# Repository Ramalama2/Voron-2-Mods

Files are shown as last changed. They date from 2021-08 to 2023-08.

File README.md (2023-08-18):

- Hey Boys & Girls, im sorry but i won't come back and don't plan to update anything as well.
- Thats why i have Archieved this Repository now.
- That way people will clearly see, that they should not expect anything here and probably switch to another/better/newer Mods that are available in the meantime.

Otherwise, it was a great time and a great community with a lot of cool people!
Cheers :-)</h1></center>

------------------------

<h1 align="center">Mod Index:</h1>
<table align="center">
  <tr>
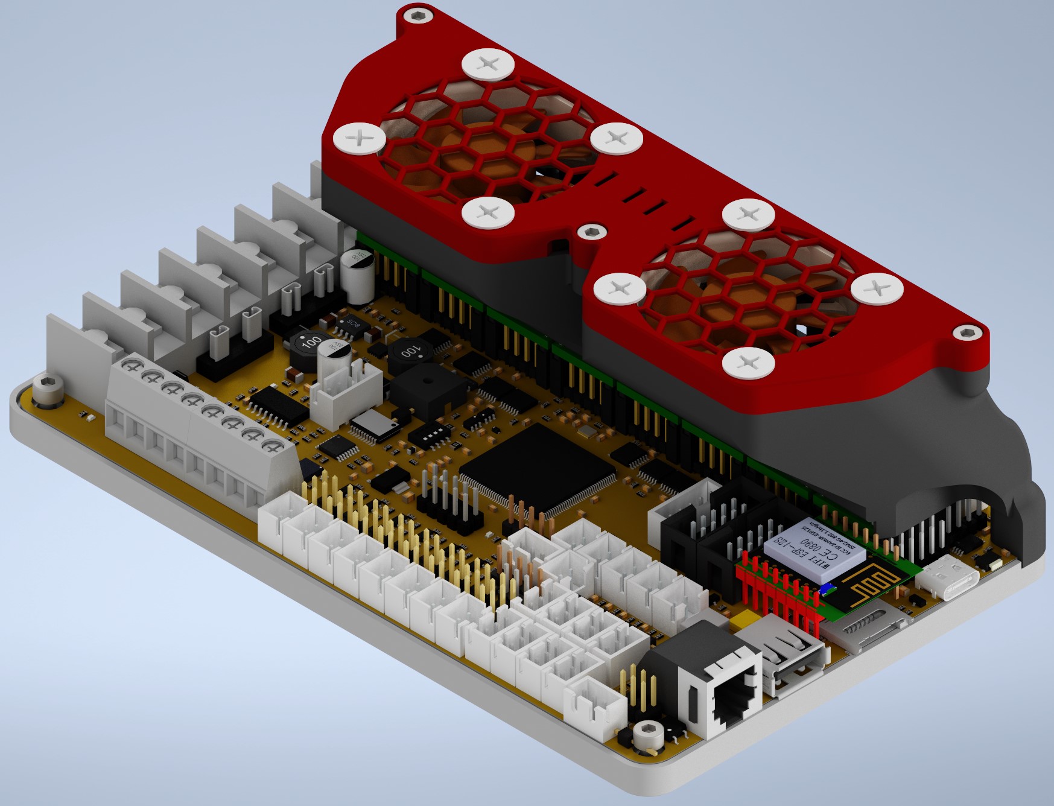
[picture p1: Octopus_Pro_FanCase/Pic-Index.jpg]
    <td align="center"><a href="./Octopus_Pro_FanCase">Octoglasses<br></a></td>
  </tr>
  <tr>
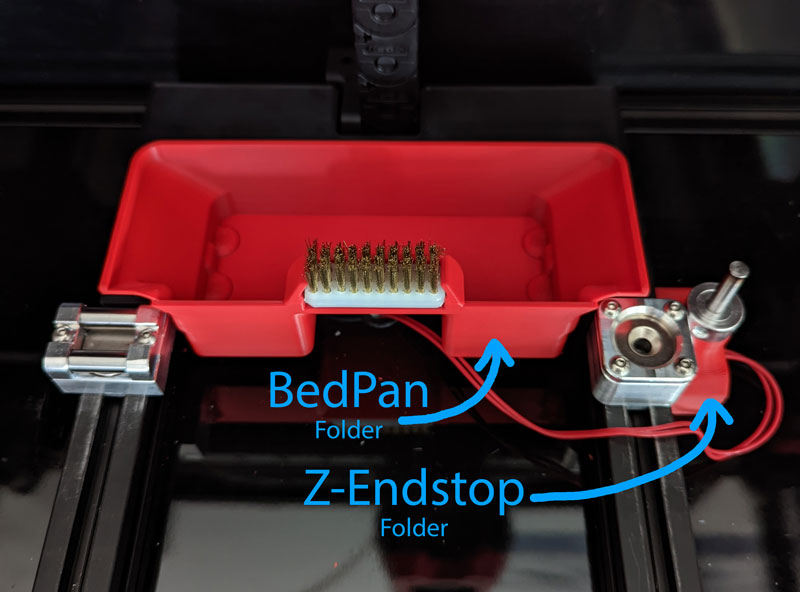
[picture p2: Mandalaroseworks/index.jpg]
    <td align="center"><a href="./Mandalaroseworks">Mandalaroseworks<br></a></td>
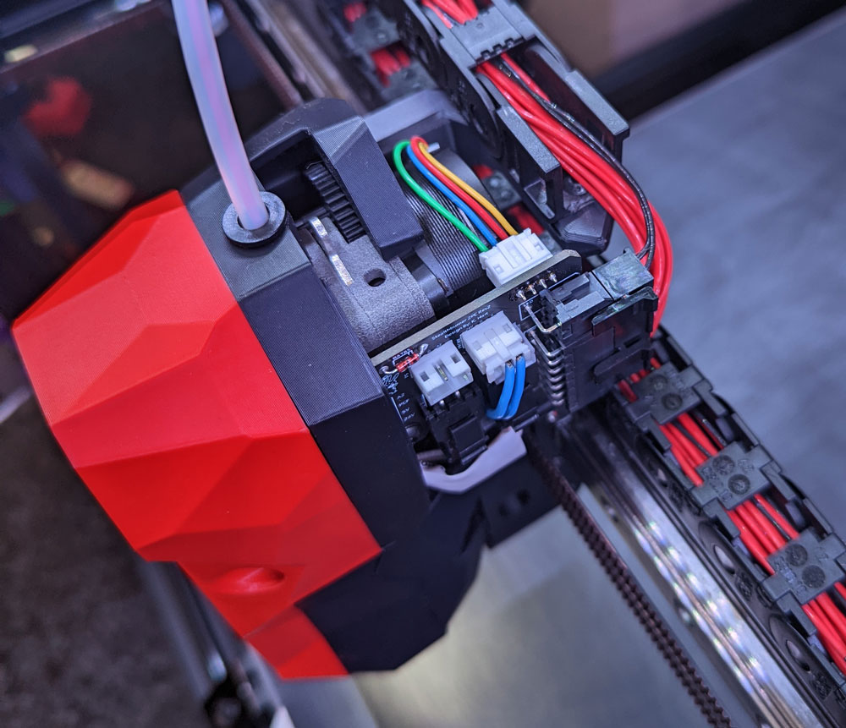
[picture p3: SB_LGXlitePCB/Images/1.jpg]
    <td align="center"><a href="./SB_LGXlitePCB">Stealthburner LGX lite<br></a></td>
  </tr>
  <tr>
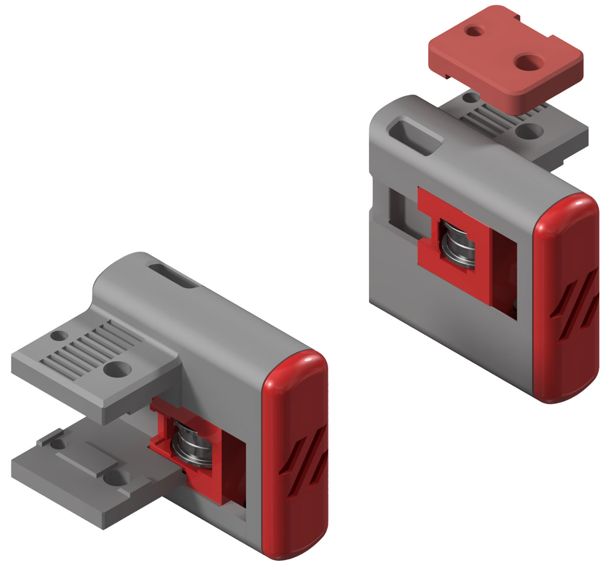
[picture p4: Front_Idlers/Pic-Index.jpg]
    <td align="center"><a href="./Front_Idlers">Front Idlers<br></a></td>
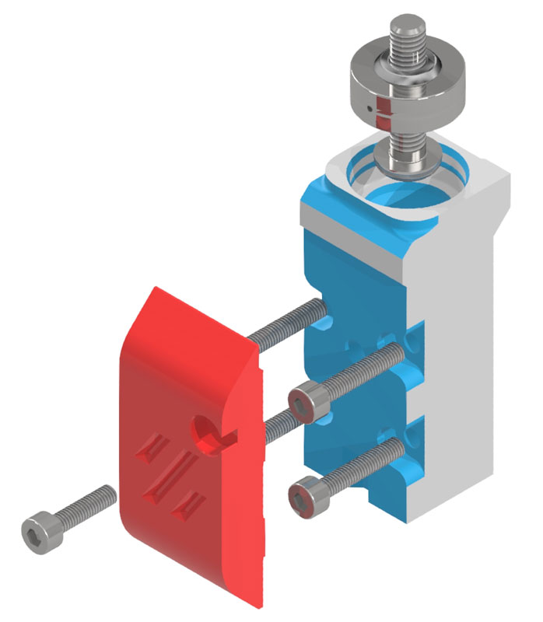
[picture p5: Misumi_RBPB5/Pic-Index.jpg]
	<td align="center"><a href="./Misumi_RBPB5">Misumi RBPB5 (GE5C Gucci Mod)<br></a></td>
  </tr> 
  <tr>
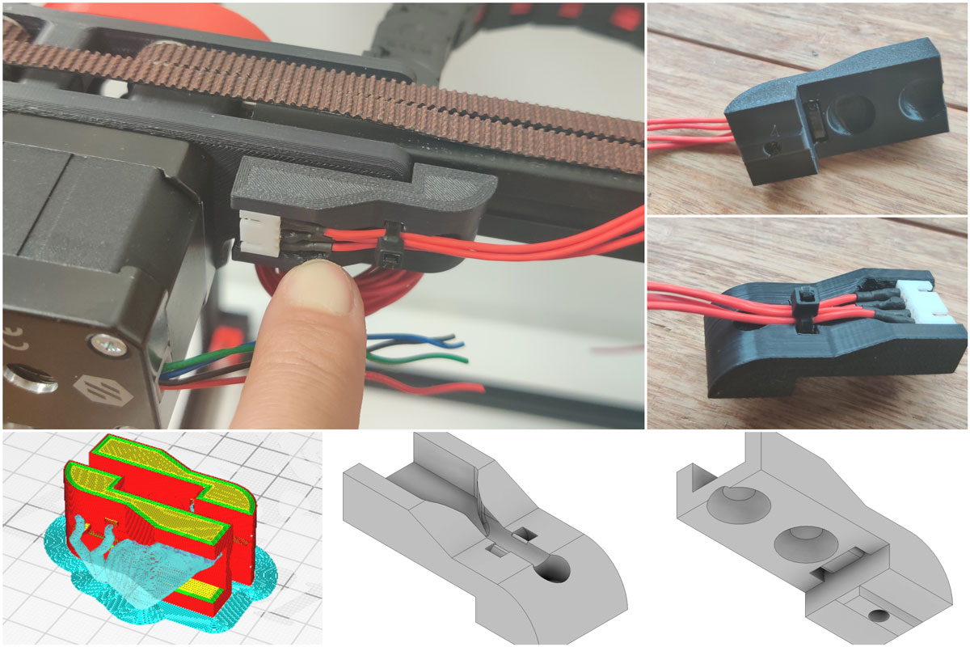
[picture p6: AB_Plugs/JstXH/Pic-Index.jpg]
    <td align="center"><a href="./AB_Plugs">AB Plugs (Jst/Microfit)<br></a></td>
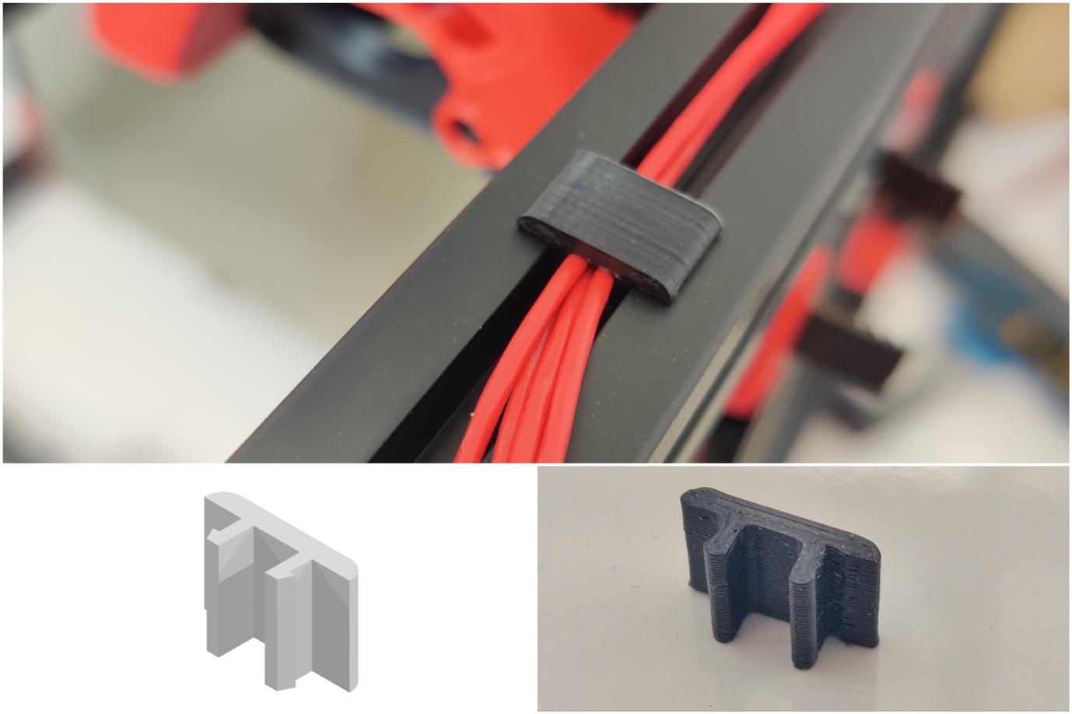
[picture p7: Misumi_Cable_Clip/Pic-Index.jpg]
	<td align="center"><a href="./Misumi_Cable_Clip">Misumi Cable Clip<br></a></td>
  </tr> 
  <tr>
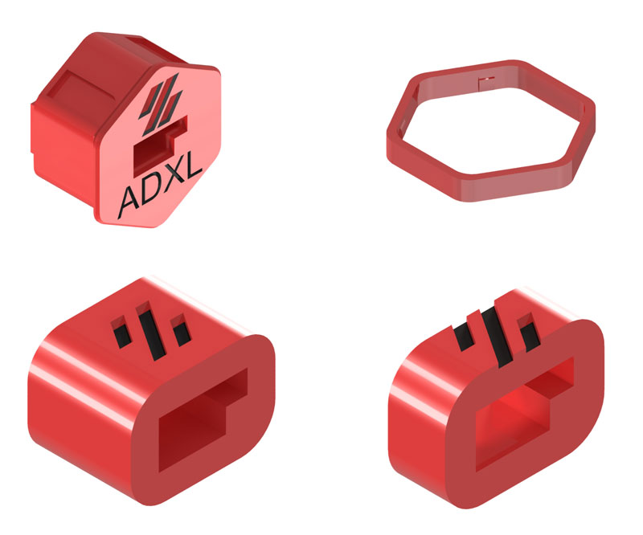
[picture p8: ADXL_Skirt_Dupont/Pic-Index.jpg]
    <td align="center"><a href="./ADXL_Skirt_Dupont">ADXL Skirt Dupont<br></a></td>
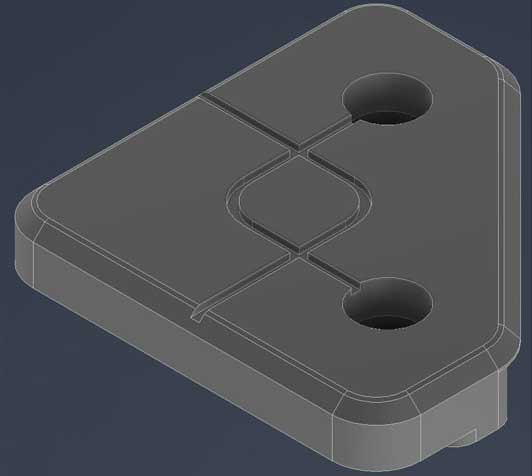
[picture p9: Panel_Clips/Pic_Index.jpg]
	<td align="center"><a href="./Panel_Clips">Panel Clips<br></a></td>
  </tr>
  <tr>
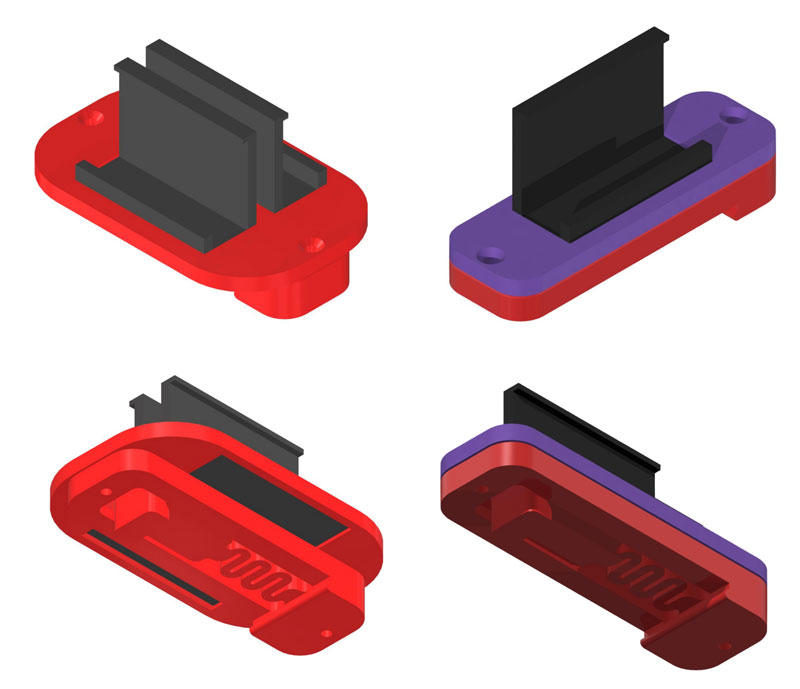
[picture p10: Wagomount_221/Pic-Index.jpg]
    <td align="center"><a href="./Wagomount_221">Wago 221 DIN Mount<br></a></td>
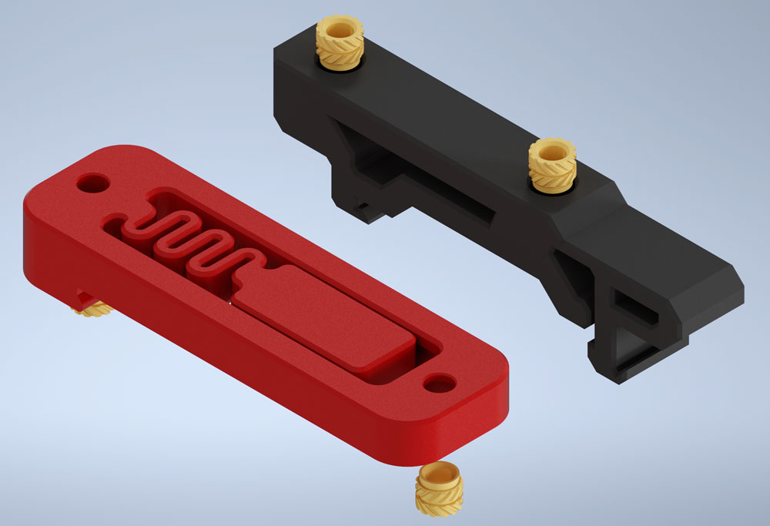
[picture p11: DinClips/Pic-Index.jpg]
    <td align="center"><a href="./DinClips">Din Clips<br></a></td>
  </tr>
    <tr>
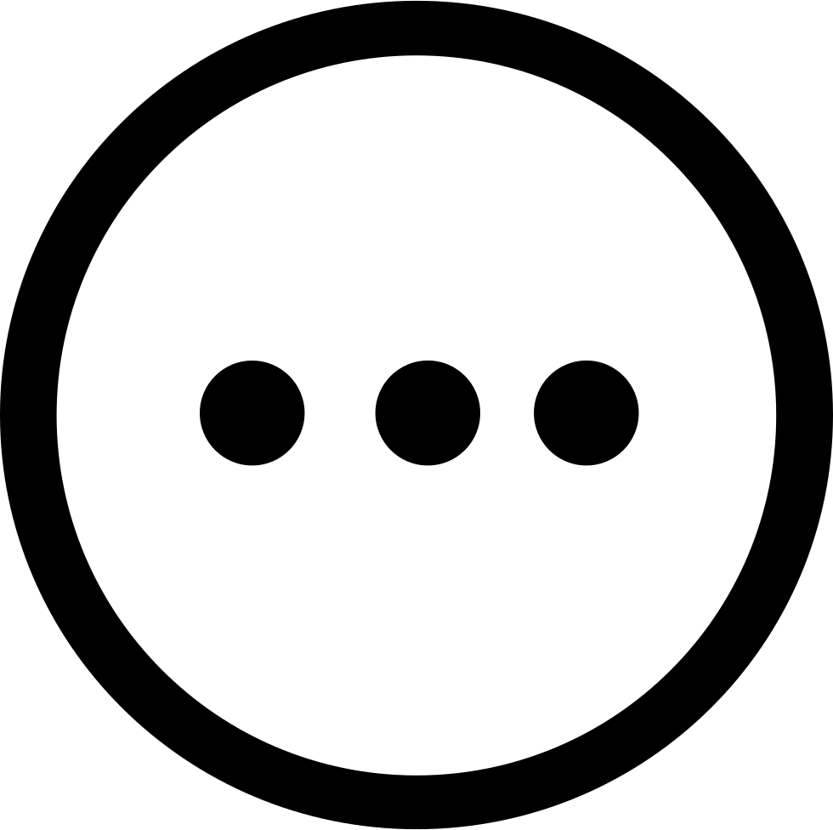
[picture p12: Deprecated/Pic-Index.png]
    <td colspan="2" align="center"><a href="./Deprecated">Deprecated Stuff<br></a></td>
  </tr>
  </table>

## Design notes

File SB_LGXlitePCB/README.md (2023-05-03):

## Changelog:
- 25.07.2022: Cable Cover, First test, please try and report back. It may be a little thin xD<br>
- 25.07.2022: <a href="./Option_without_LGXlite-FanPCB">New Option without FanPCB</a>. See this as an emergency option,<br>
this will work with the Standard FanPCB from hartk!<br>
But at least you can now get the thing running and replace later when you get the Lgx lite FanPCB.<br>
-Release (24.07.22): Release!
<details>
  <summary>
    Old Changelog
  </summary>
- Nothing yet.
</details>

#

#

#

<details>
  <summary>
    CREDITS: LOGAN!!!, Eytecz, hartk, Voron-Team & all the great people we have in our community :-)
  </summary>
* Logan: He modified hartk's Fan-PCB to make this Project working at all! Thanks Logan!!!<br>
* Eytecz: <a href="https://github.com/Eytecz/LGX_Lite_Stealthburner_CW2_style_mount">Original SB-Lgxlite</a>, he made the work, i modified it only for the 2-Part PCB!<br>
* hartk: For the beatiful 2-Part PCB :-)<br>
* Voron-Team: Yeah, without you Guys, nothing were possible here :-)<br>
* Community: Feelingwise discord is a Place filled with only nice and always helpful People! A special thanks to all of them, i personally just love everyone there!<br>
</details>

<details>
  <summary>
    Print Settings:
  </summary>
- Default Voron settings, correct orientation, no supports needed!<br>
</details>

<details>
  <summary>
    Where can i get the Fan-PCB from?:
  </summary>
- JlcPCB: All you need is the <a href="./PCB">Gerber File</a><br>
- Discord: Gi7mo!#4618 -> He has them already on Stock! (Germany/EU)<br>
- Note: The mainpcb is default hartk, only the fanpcb changed a bit!<br>
</details>

<details>
  <summary>
    BOM:
  </summary>
- 12x M3 Threaded Insert<br>
- 2x DIN 562 - M3<br>
- 2x ISO 7380 - M3 x 6<br>
- 2x DIN 912 - M3 x 5<br>
- 5x DIN 912 - M3 x 12<br>
- 3x DIN 912 - M3 x 25<br>
- 1x DIN 912 - M3 x 20<br>
- 1x DIN 912 - M3 x 8<br>
- 1x UM2 4mm Connector<br>
</details>

<details>
  <summary>
    Description:
  </summary>
- This is basically Eytecz LGX-Lite mount, modified for the 2-Part PCB and some other Updates<br>
- The Pictures should as always be self-explanatory!<br>
- There are 2 options: CW1 Carriage or CW2 Carriage! I do highly recommend the CW1 Carriage, because on the CW2 the only change are the inserts from the front, because the CW2 extruder needs that. Those inserts will likely fall out after a time! As this is the only change, i highly recommend the CW1 Version!<br>
- PCB_Mount_Offset_0.6mm and PCB_Mount_Default: Try first the default version, if you issue problems try the "Offset Version", it puts the PCB 0,6mm further back if the connector isnt seamless with the front of the Mount.<br>
- Optionally for best compatibility, you can print [Optional]_Stealthburner_Body. It is not needed, but it will make fittings minimally better!<br>
- Its recommended to cut the pins flush on the Hartk PCB! They can or are in most cases too long.<br>
</details>

## Pictures:
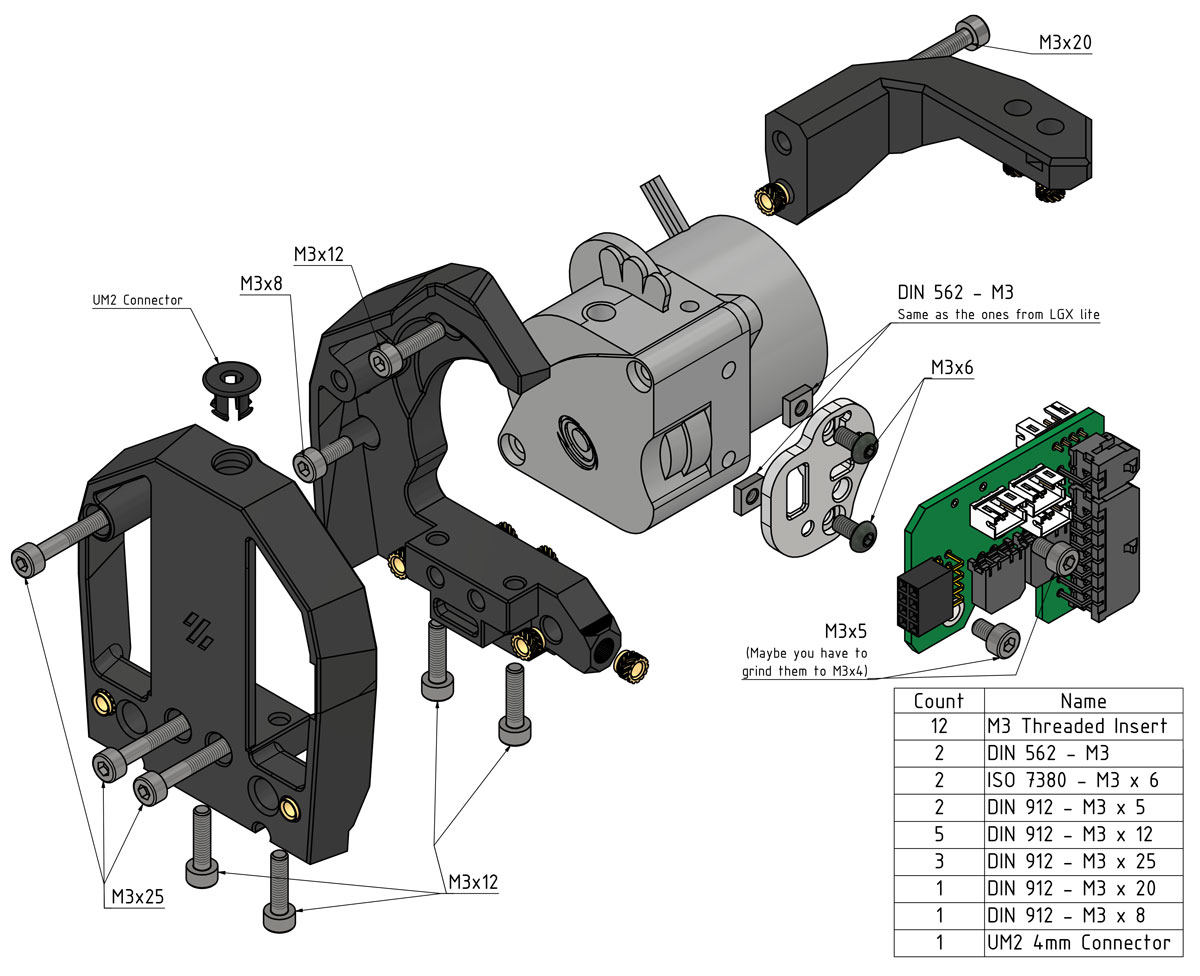
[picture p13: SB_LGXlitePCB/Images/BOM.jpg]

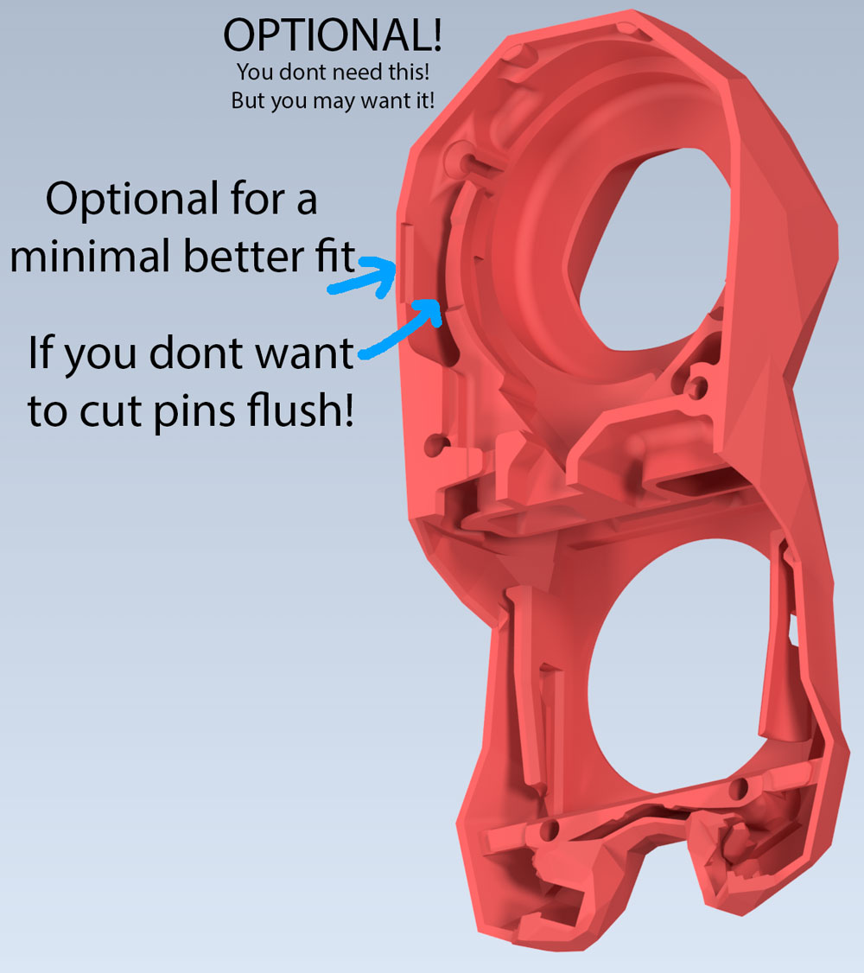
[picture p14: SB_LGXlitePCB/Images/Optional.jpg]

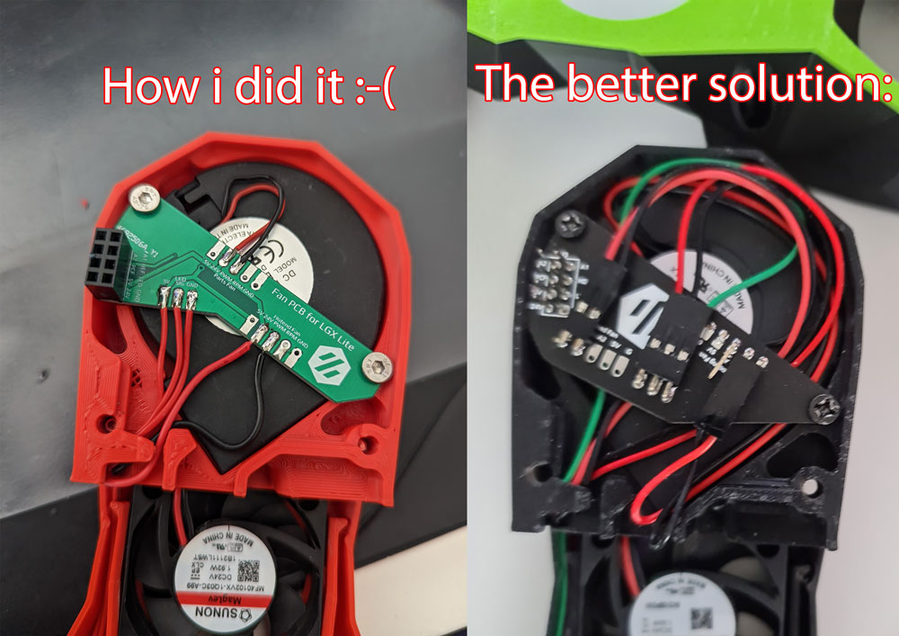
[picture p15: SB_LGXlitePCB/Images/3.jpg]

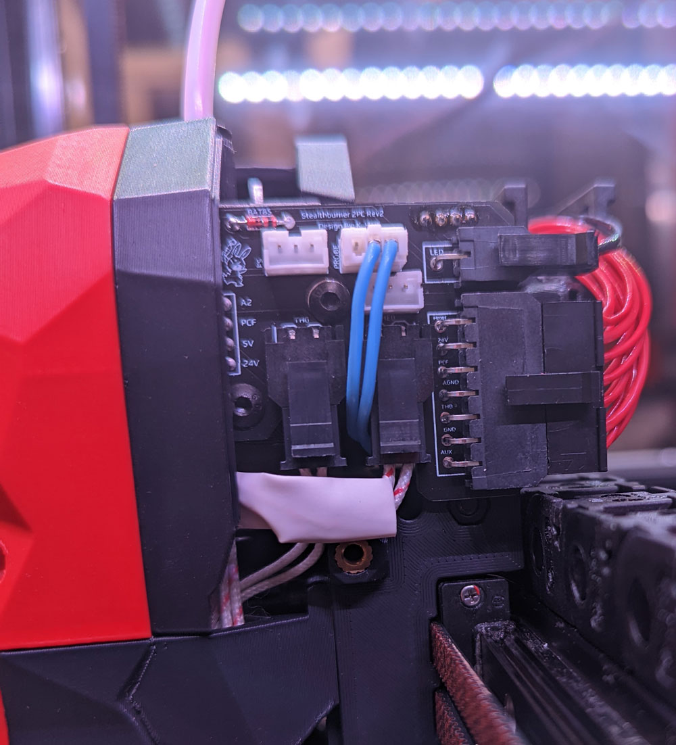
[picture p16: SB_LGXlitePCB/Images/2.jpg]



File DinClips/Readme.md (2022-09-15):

## DIN Clips/Brackets
### Credits:
- Voron-Team: Its the default generic DIN Clips, but modified!<br>

#### Changelog:
- 15.09.2022: New-Style Dinclips with M3-Inserts<br>
- 11.09.2022: M3 Version with and without Inserts<br>
<details>
  <summary>
    Old Changelog
  </summary>
-Release (01.09.2021): Release!<br>
</details>

#### Printing:
- Default voron settings, correct orientation, no supports needed!<br>

#### Bom:
- 2x M2x10 Self-tapping Screw<br>

#### Description:
- All Dinclips/Brackets are compatible with their original counterparts. The hole distances are the same.
- To make the M3 ones compatible with your mounts, you just have to drill up your holes to 3mm for the M3 screws instead of those Self-Tapping M2 Screws.
- Stiffer generic Din Bracket (same as the one for the pi, but it sits much tighter on the din rail. I found the voron ones a bit wobbly on the din rails) You can use this bracket for everything else.

#### Pictures:


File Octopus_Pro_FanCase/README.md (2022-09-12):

<h1 align="center">Octopus Pro FanCase aka Octoglasses</h3></p>
<br>
<details>
  <summary>
   Changelog: Release (11.09.22): Octoglasses
  </summary>
- Nothing Yet! <br><br>
</details>

#
<br>
<details>
  <summary>
    CREDITS: Voron-Team for the Din-Clips & Gi7mo! for <a href="https://github.com/Gi7mo/TinyFan">TinyFan</a>!
  </summary>
* Voron-Team: Yeah, without you Guys, nothing were possible here :-)<br>
* Gi7mo!: Big thanks to you for the TinyFan! It's like a must have for this Project!<br>
* Community: Feelingwise discord is a Place filled with only nice and always helpful People! A special thanks to all of them, i personally just love everyone there!<br>
</details>

#
<br>
<details>
  <summary>
    Print Settings:
  </summary>
- Default Voron settings, correct orientation, no supports needed!<br>
</details>

#
<br>
<details>
  <summary>
    BOM:
  </summary>
- 7x M3x8 SHCS<br>
- 4x M3x8 BHCS<br>
- 2x M3 Nuts<br>
- 5x M3-Inserts<br>
- 2x <a href="https://github.com/Ramalama2/Voron-2-Mods/tree/main/Stiffer_DinMount">Stiffer DIN Mount M3 (Insert)</a><br>
- 2x Noctua NF A4x10 12v PWM (Any Other 4010 12v Fan is fine either)<br>
- 8x ST-FANSCREW (Comes with Noctua Fans already)<br>
- 1x Heasink for the STM32Fxxx Chip<br>
- 1x <a href="https://github.com/Gi7mo/TinyFan">TinyFan</a>, you can get one from Gi7mo! in Germany. I highly recommend one for Noctua Fans!<br>
</details>

#
<br>
<details><summary>Assembly: <a href="./Manual.pdf">Manual PDF</a> or <a href="./Manual/">Manual Images</a></summary>
- <a href="./Manual.pdf">Manual as PDF</a><br>
- <a href="./Manual/">Manual as Images</a>
</details>

#
<br>
<details>
  <summary>
    Description:
  </summary>
- Why:<br>
- The 5160 Pro Drivers are getting extremely hot! You need to cool them!<br>
- I highly recommend the <a href="https://github.com/Gi7mo/TinyFan">TinyFan from Gi7mo!</a><br>
- The FanCase has Cablehole exits at the back, for the TinyFan.<br>
- You don't need it, but its amazing for Noctua fans to see RPM and control those Correctly with a PWM signal.<br>
- Every Heatsink of the 5160 Pro Drivers fits! I have tested Fysetc 5160 HV/BTT 5160 Pro v1 and the new v1.3 either!<br>
- Don't even imagine to use drivers without heatsinks, those fans won't save your drivers life!<br></details>

#

<br>
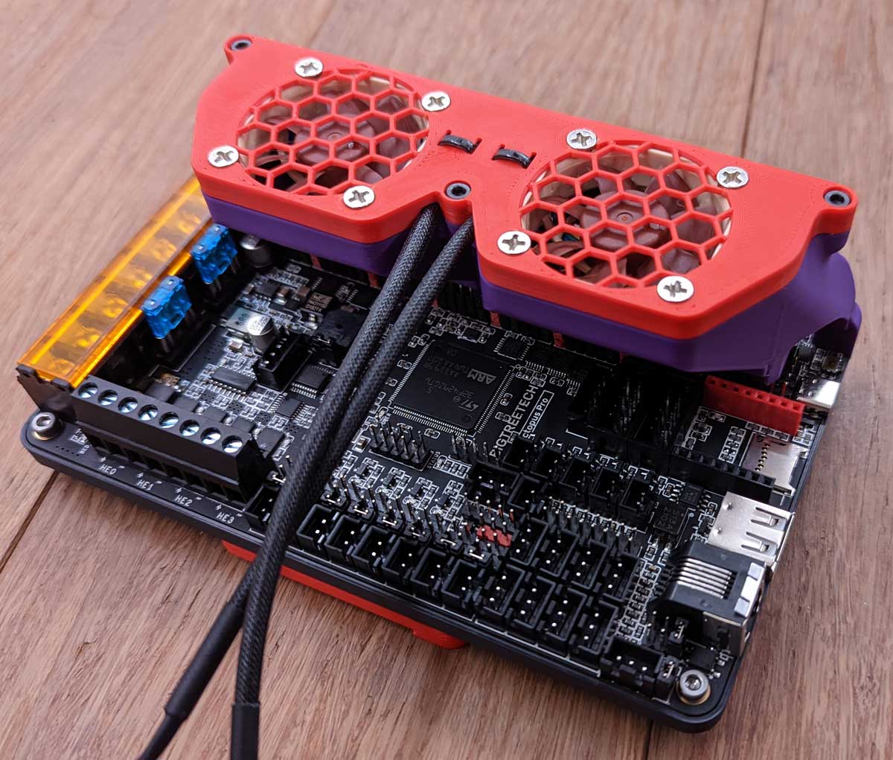
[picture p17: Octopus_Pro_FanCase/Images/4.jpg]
<br>
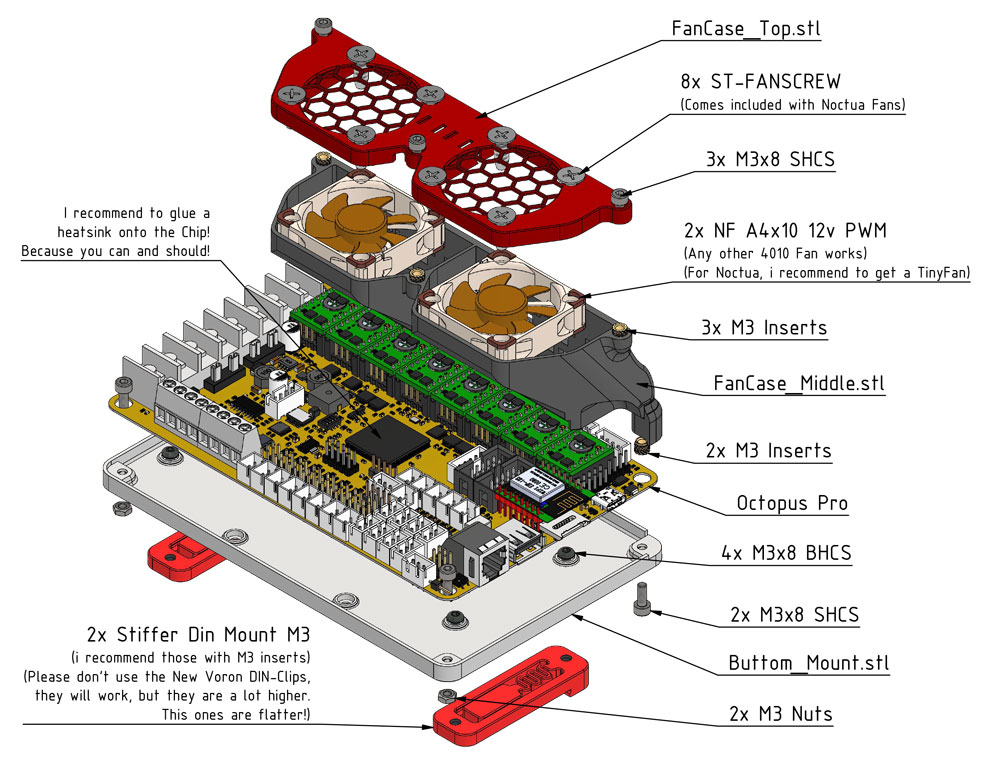
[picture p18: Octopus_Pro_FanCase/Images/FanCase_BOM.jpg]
<br>
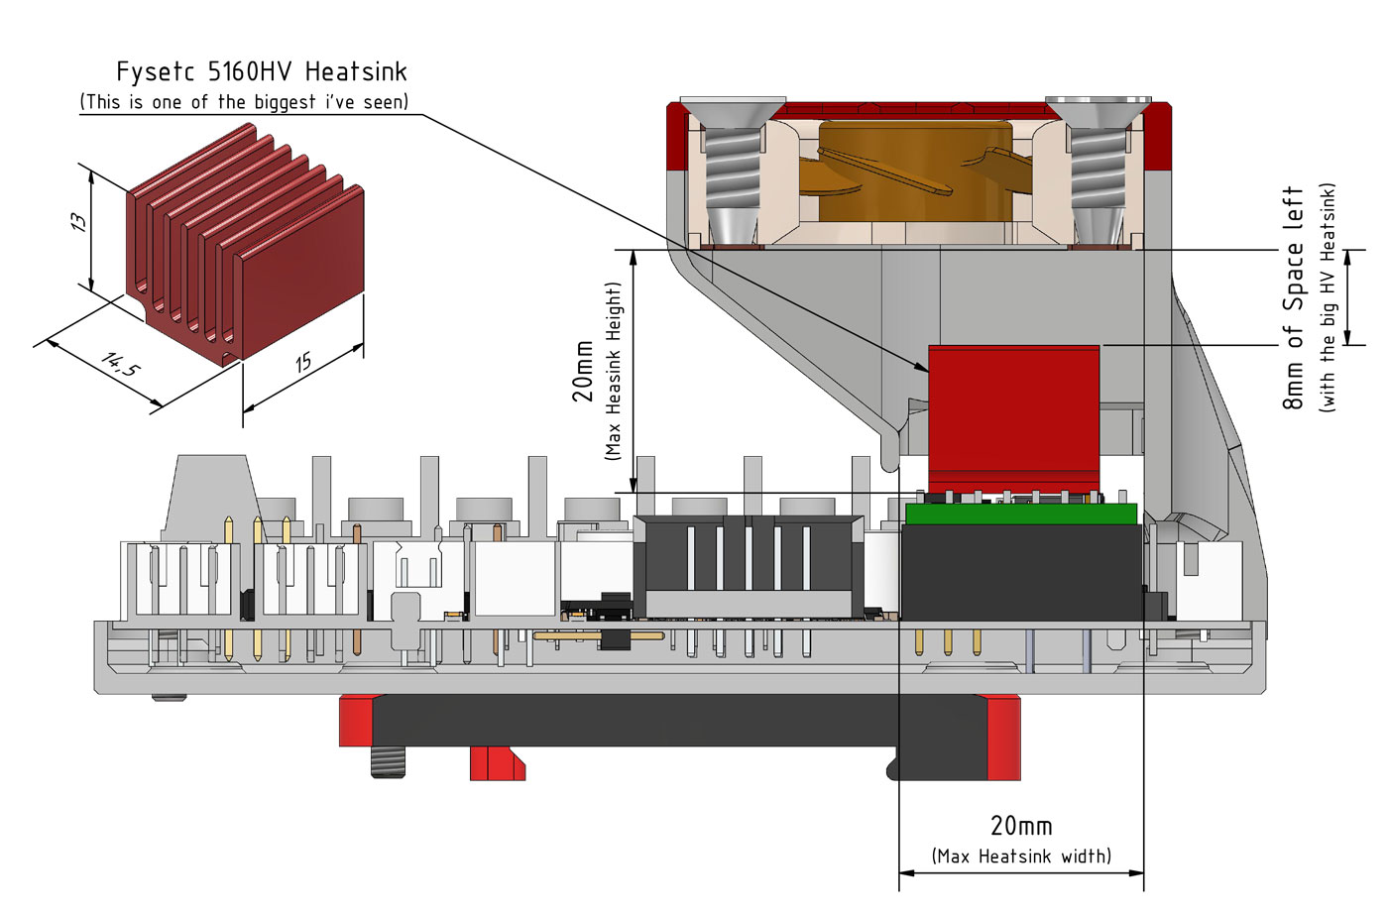
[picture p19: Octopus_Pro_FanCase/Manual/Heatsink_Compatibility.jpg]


#

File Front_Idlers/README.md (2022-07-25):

## Changelog:
- Update (25.07.22): Nipplefix, hopefully the centering pins that tend to break, are fixed now. Try the "Nipplefix" version :-)
- Update (22.03.22): A Special Thanks to TadasMit, who bought you the Trident Version of the Idlers! There is more done as just removing the holes, its generally perfectly adopted for the Trident. So if you still using the 2.4 Idlers on a Trident, its time to upgrade! Another Note: Those who are using his Idlers (downloaded from the Issue thread where he posted them, don't need to Change anything!). There are small updates to 2.4 as well, just ignore those, these updates are only for first timers, to clear things a bit up. So nothing changed there other as names!
<details>
  <summary>
    Old Changelog
  </summary>
- Update (02.09.21): STLs available for testing! Please print and report issues!<br><br>
- Update (03.09.21): Added "Upper" Z-Belt-Clamp, i need to redesgn the sliding mechanism. Still unhappy about it.<br><br>
- Update (04.09.21): Added the final version, added all CAD/STL Files, now needs longtime testing. But it should be ready to use! From this point on, i will only update if i or someone else find issues!<br><br>
- Update (05.09.21): Improved minimally tolerances. (This is the final Version!). Feel free to use it!<br><br>
- Update (06.09.21): Corrected the mounting Holes, better belt alignment for clamping! (Housing & Z-Belt-Clamp-Upper)<br><br>
- Update (27.09.21): Cover Release, the Alpha ones didn't fitted correctly. Tested Front-Idlers and using now! They are a pain in the butt to mount, since you have to push them from the end of the extrusion on. But the work absolutely perfect! Added a Housing for a M3x40mm screw, i had some nice ones that i preferred simply.<br><br>
- Update (08.10.21): Just to take out some confusion: Front-Idlers_Housing and Front-Idlers_Housing-40mm, are the same, there is no difference other as, the default is for 30mm screws and the 40mm for 40mm screws. Use simply the one which you have screws for!<br><br>
- Update (04.11.21): Thanks to Long, there is now an Inlet with a bigger Pinhole, we recommend the 5.1 Version. Something else: Ignore the GE5C version, this is just a test, you can use the normal Version. When i get a bit more time, i will update the idlers and make some nice Covers etc... Will give them a bit love. But rn, i have no time, sry :-(<br><br>
- Update (10.11.21): GE5C "Offset" Version... There is a dot at the back, the dot should point to the GE5C Z-Joint side. Use hartk's z-belt-clamp-lower: https://github.com/hartk1213/MISC/blob/main/Voron%20Mods/Voron%202/2.4/Voron2.4_GE5C/STLs/%5Ba%5D_z_belt_clamp_lower_x4.stl and my "Front-Idlers_Z-Belt-Clamp-Upper-" Left & Right!<br><br>
</details>

#

#

#

<details>
  <summary>
    CREDITS: Voron-Team, Henrikssn, Long, TadasMit & all the great people we have in our community :-)
  </summary>
* Voron-Team: Yeah, without you Guys, nothing were possible here :-)<br>
* Henrikssn: For testing & improvement suggestions & for the cool Cover he made!<br>
* Long: For the testing and suggesting improvements! Check out the <a href="https://github.com/mandryd/VoronUsers/tree/master/printer_mods/Long/Mantis_Dual_5015">Mantis</a> & <a href="https://github.com/mandryd/MantisUsermods/tree/main/Usermods">Mantis Mods</a>!<br>
* TadasMit: The one that took the time and made a Version for all the Trident People out there! Special Thanks!<br>
* Community: Feelingwise discord is a Place filled with only nice and always helpful People! A special thanks to all of them, i personally just love everyone there!<br>
</details>

<details>
  <summary>
    Print Settings:
  </summary>
- Default Voron settings, correct orientation, no supports needed!<br>
- The inlet has 53° overhangs; you want to print the inlet with higher fan speed. (At least 50% in an enclosed printer for ABS!)<br>
- Try to slide the Inlet in the housing, optimally it should slide fine and have almost no play. In worst case, print the inlet with even more fan and slower!<br>
- Keep in mind, no play is impossible, but there should be only minimal axial play, only in the front of the inlet.<br>
- Everything else should be a breeze to print!<br>
- Seam: You don't want the seam outside, it will look ugly. Rotate the seam to the extrusion mounting side! (Should be "right"), Check the Picture:<br>
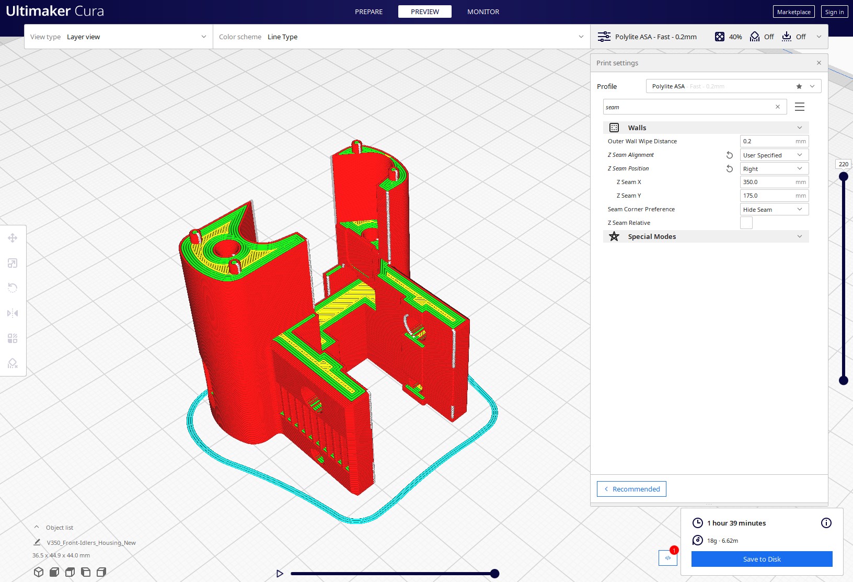
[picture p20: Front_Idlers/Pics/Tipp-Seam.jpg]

</details>

<details>
  <summary>
    BOM: (Multiply by 2 for Left+Right)
  </summary>
- 2x M3x30 SHCS (Full threaded) or M3x40 SHCS (Full threaded)<br>
- 1x M3x8 or M3x10<br>
- 2x M3 Washer<br>
- 2x M5 Washer<br>
- 2x M3-Inserts<br>
- 2x F695zz or F695-2RS bearing. (You should have this on your actual idler already)<br>
- 1x 5x18 Pin (g6)<br>
- 2x 3x6 Magnets<br>
</details>

<details>
  <summary>
    Tips:
  </summary>
Don't even think about buying the 5×18 Pins.<br>
You will need those pins later everywhere anyway.<br>
Additionally, most pins that you buy come in H7 and not G6,<br>
which means they are slightly too thick and you will have to grind them down to fit the bearing.<br>
Instead, do yourself a favour and <a href="https://a.aliexpress.com/_mLkPTBH">buy this one instead</a>.<br>
This one comes in G6 (so no grinding down needed for the bearing to fit) and you get them in 500mm super cheap.<br>
You simply have to cut them to size.<br>
Buy directly 2 500mm ones, because you will need them for a lot of other mods too!<br>
</details>

<details>
  <summary>
    Assembly:
  </summary>
- Insert the M5 shims and the F695zz bearings one by one and push the pin flush inside. (One by one, because there isn't enough place to put them all together inside)<br>
- As next step:<br>
- The M3 inserts, doesn't mean to be inserted hot. Just take the Housing, Housing-Cover, 2x M3 Shims and 2x M3x30 screws, assemble it together and screw the m3 inserts simply inside with the tension of the screws. (They will push fit inside the hole while screwing)<br>
- The rest is self explanatory.<br>
- About the covers, I know that the holes there are big, far bigger than needed. But I will release better covers later and maybe different designs.<br>
</details>

<details>
  <summary>
    Description:
  </summary>
- The Problem: -<br>
1. The default idlers have the issue, at least for me, that the tensioning screw splits the 2 pieces apart.<br>
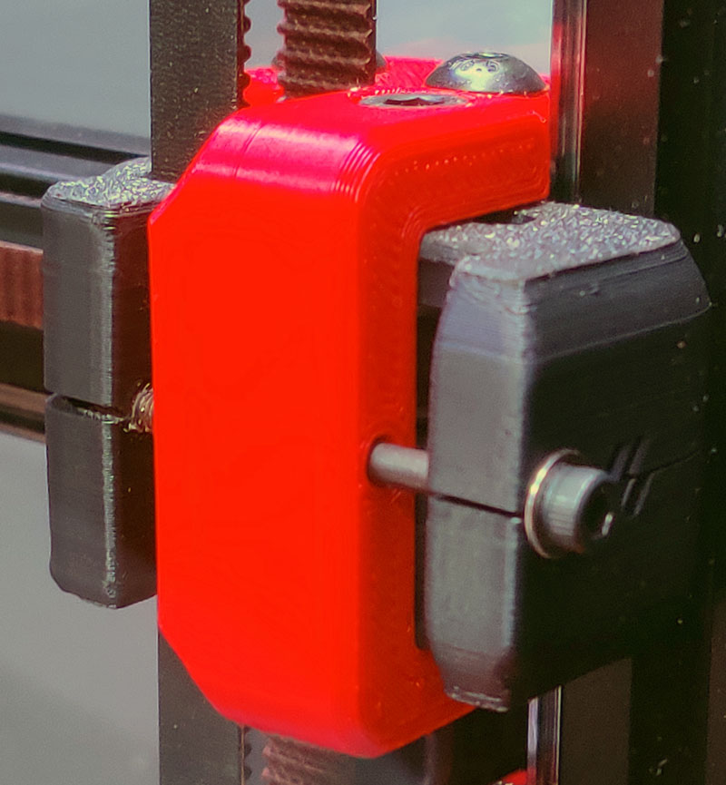
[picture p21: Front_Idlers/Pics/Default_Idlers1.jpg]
<br>
2. The screw where the bearing sits on, gives the bearing a lot of play. This adds to inconsistencies, not much, but why shouldn't we improve it? Check the video: https://youtu.be/_tG0CdSuppk<br>
<br>
- Mod: -<br>
1. Fixes all issues above.<br>
2. It's stiffer.<br>
3. The idlers are 9mm thinner (a solution for Mantis owners).<br>
4. I can't help myself, but I like the default idlers look. This ones looks in my opinion less vorondesign and more streamlined. I made some covers, but please feel free to open issues or whatever on GitHub with your opinions, how to give them the Voron "touch" or make them more beautiful.<br>
</details>

#

#

#

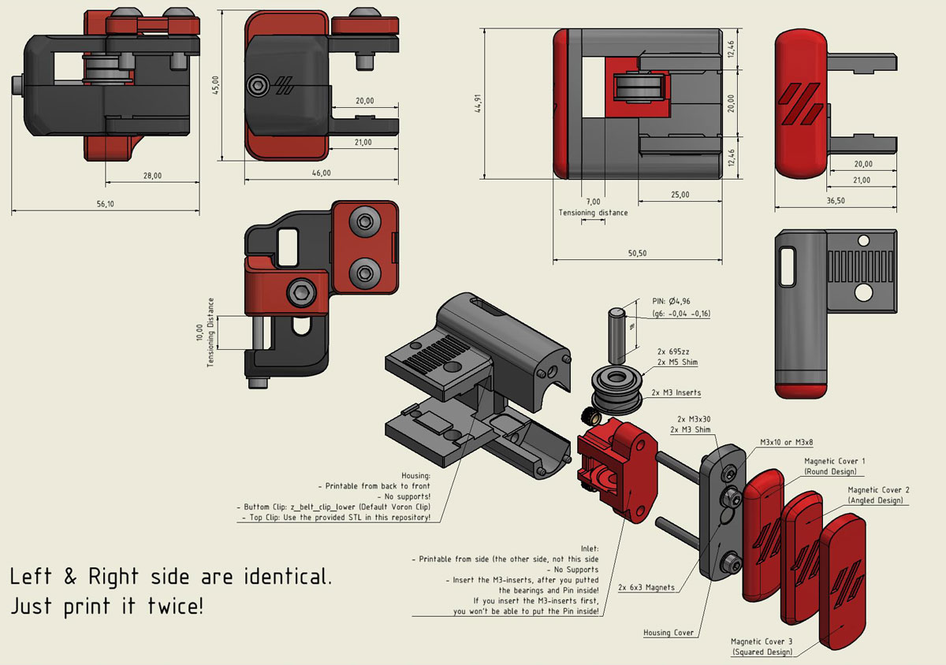
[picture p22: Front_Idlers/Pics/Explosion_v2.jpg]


#

#

#

## Mods (Covers):
- Cover by henrikssn:
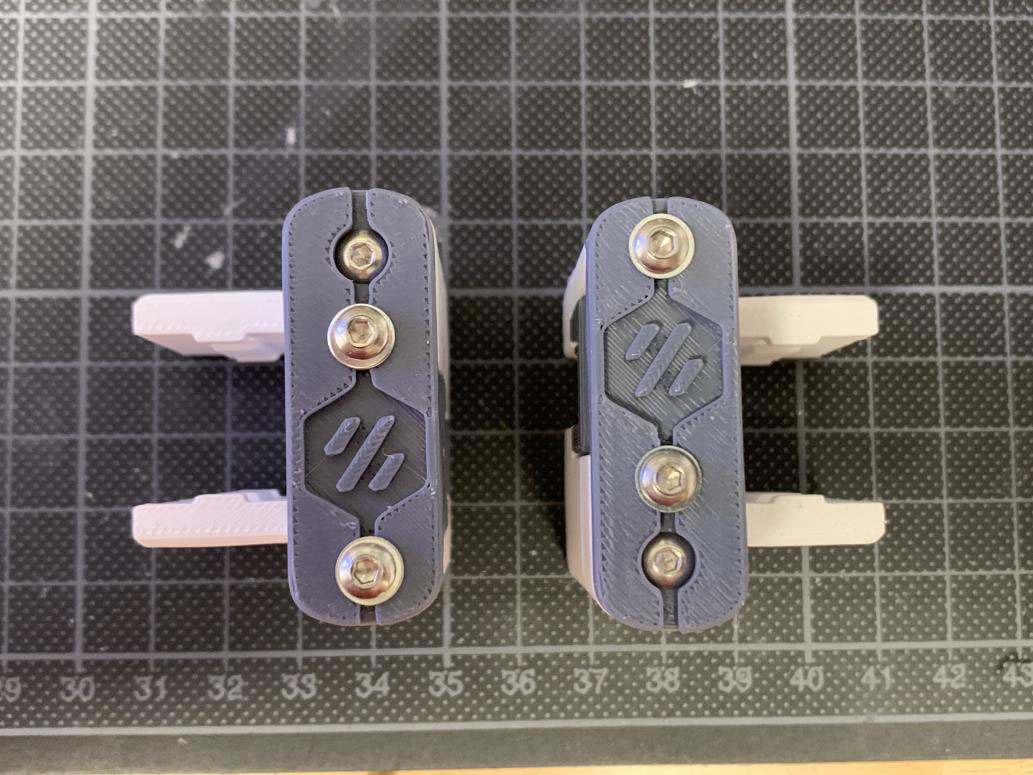
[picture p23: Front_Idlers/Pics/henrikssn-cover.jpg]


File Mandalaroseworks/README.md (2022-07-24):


<h1 align="center">Index:</h1>
<table align="center">
  <tr>
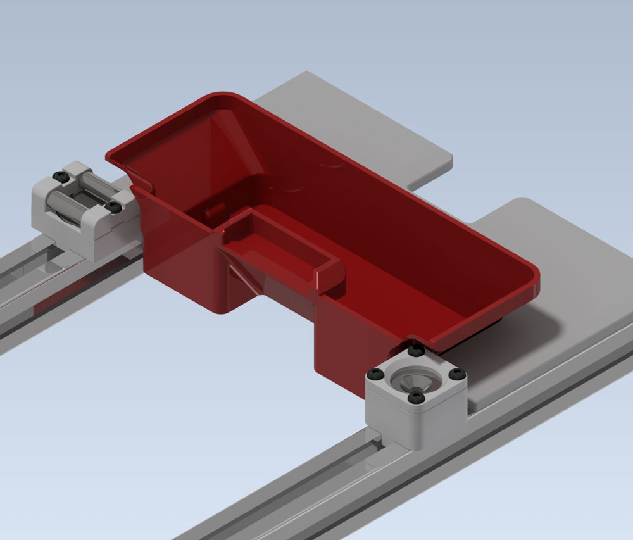
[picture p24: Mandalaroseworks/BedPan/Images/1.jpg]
    <td align="center"><a href="./BedPan">BedPan<br></a></td>
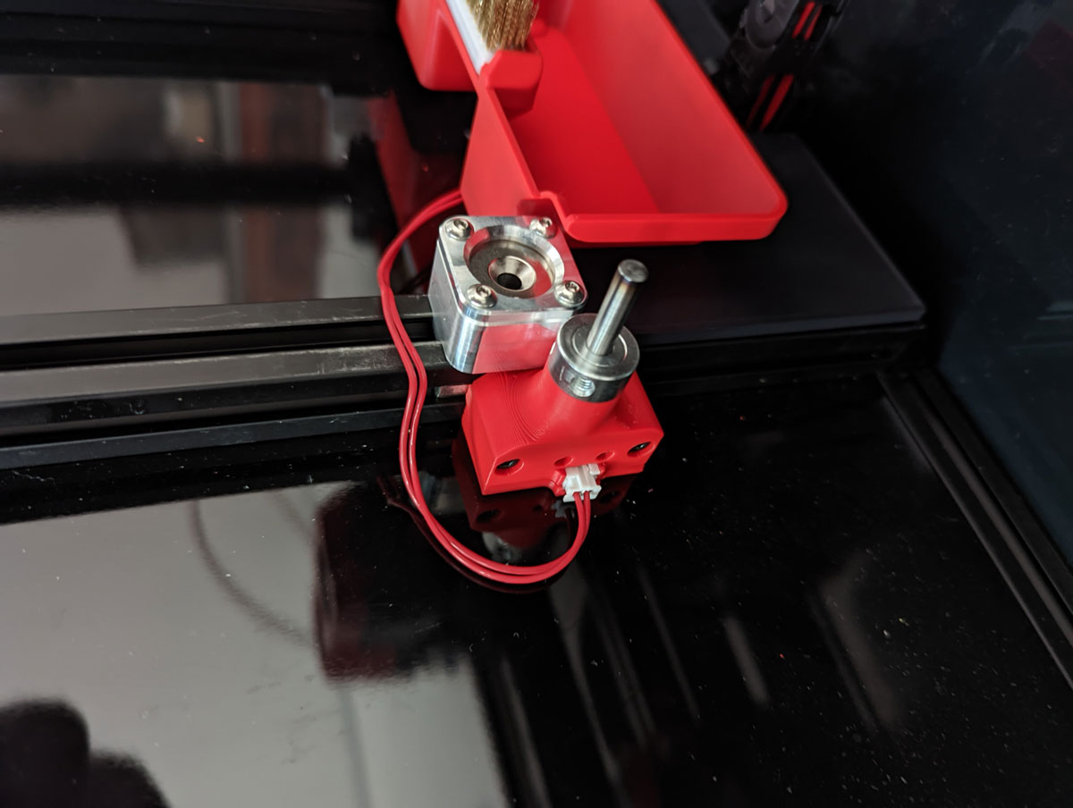
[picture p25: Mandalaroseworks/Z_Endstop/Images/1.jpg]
	<td align="center"><a href="./Z_Endstop">Z-Endstop<br></a></td>
  </tr>
</table>

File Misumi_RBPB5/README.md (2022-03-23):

# UPDATE
- 23.03.2022: Made the tolerance for the Z-Joint (Inventor Ipt file) parametric and added a version with 0,15mm tolerance for the RBPB5 Bearing!
- 27.09.2021: Final Release of CAD & STL Files! Please keep in mind that i need to update descriptions. The BOM is still correct!
- Please keep in mind, i didn't updated the pictures, the Z-Joints are looking a bit different now!

## Misumi RBPB5 (Gucci GE5C)
##### Credits:
- @hartk1213 [Original GE5C Mod](https://github.com/hartk1213/MISC/tree/main/Voron%20Mods/Voron%202/2.4/Voron2.4_GE5C "Original GE5C Mod") (He has too much nice things, please visit his Github Page)
- His Design is made for GE5C and Igus ELGM-05
- He inspired me for this here and many more things :-)

###### Printing:
- Default voron settings, correct orientation, no supports needed!

###### Bom: (Multiply with 4 for all corners)
- 1x Misumi RBPB5
- 1x DIN433-M5 (Shim) (DIN125 will work either, but DIN433 are slightly smaller shims, those allow more tilting!)
- 1x M5x22 (BHCS/ISO 7380)
- 1x M3x12 SHCS
- 4x M3x16 SHCS
- 4x 6x3 Magnets (Magnetic Version)

- The M5x22 doesn't exists. So buy an M5x25 and grind it down to 22! Optionally (i recommend) to thind the screwhead down to 8-8.5mm diameter, this will allow more tilting! Simply put the screw on your drilling machine, turn it on and use a drehmel to grind the head down. Its easy!

###### Description:
- The whole reason for this is, that GE5C bearings have some play in them. Igus ELGM05 are a lot better, but i wanted something Gucci and even stiffer with more tilting.
- Misumi mentions in the specsheets max 0,035mm axial play. Igus and GE5C have no axial play specifications. (But igus have actually no play)
- This means for me, that with some Grease (Mobilux EP1/EP2), should remove almost all play and the uneven Gantry (it will always press the bearings outside/inside), will do the rest.

###### Update:
- After a lot of iterations and a lot of headaches, its finally done. Now i can finally tell the difference, why you probably want to do this either: you will get a lot stiffer gantry that is able to tilt freely.
- ADXL tests will follow, need to fix my printer first again, my accelerations made some screws and inserts falling out xD 

###### Pictures:
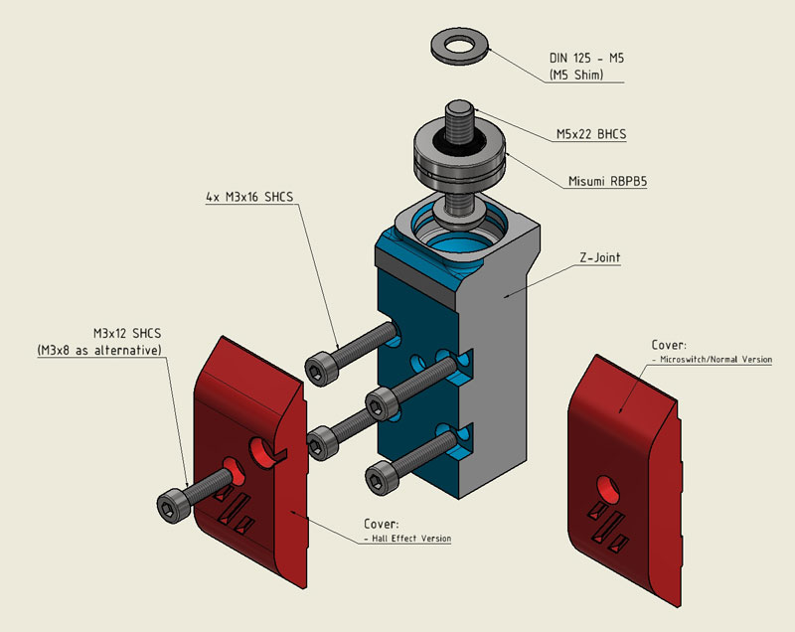
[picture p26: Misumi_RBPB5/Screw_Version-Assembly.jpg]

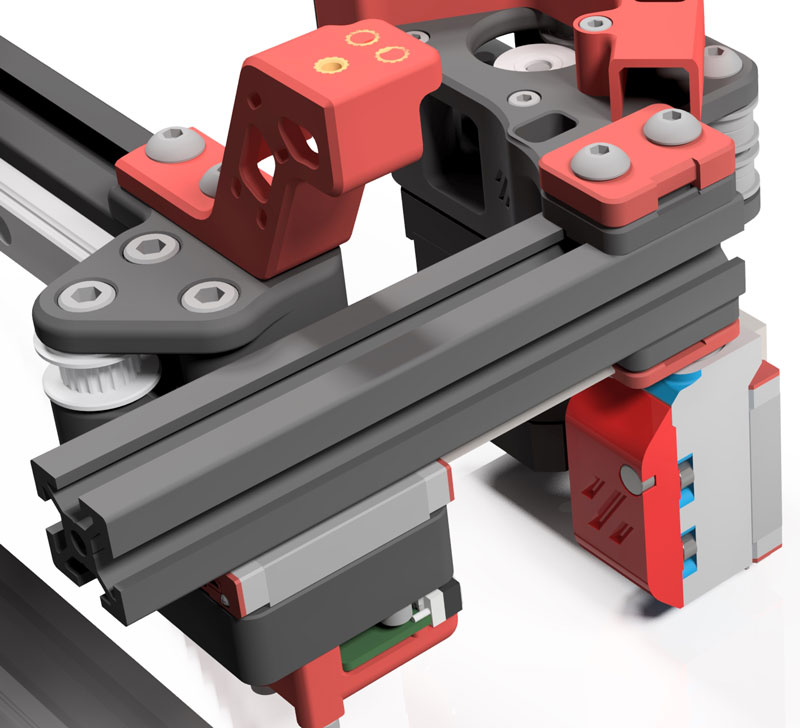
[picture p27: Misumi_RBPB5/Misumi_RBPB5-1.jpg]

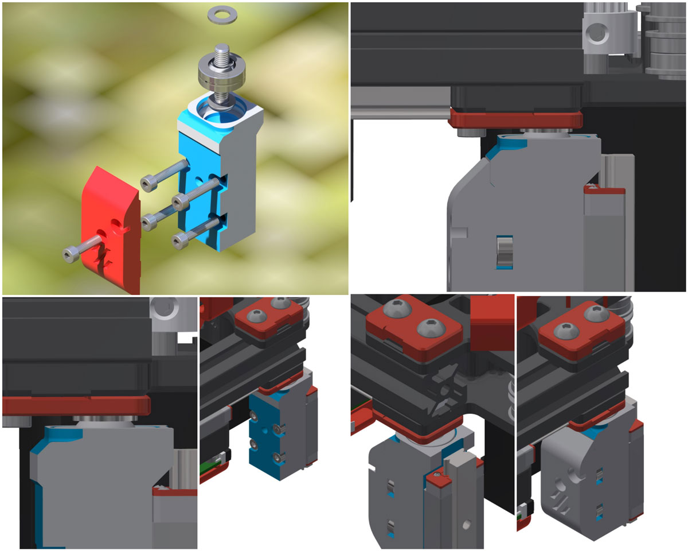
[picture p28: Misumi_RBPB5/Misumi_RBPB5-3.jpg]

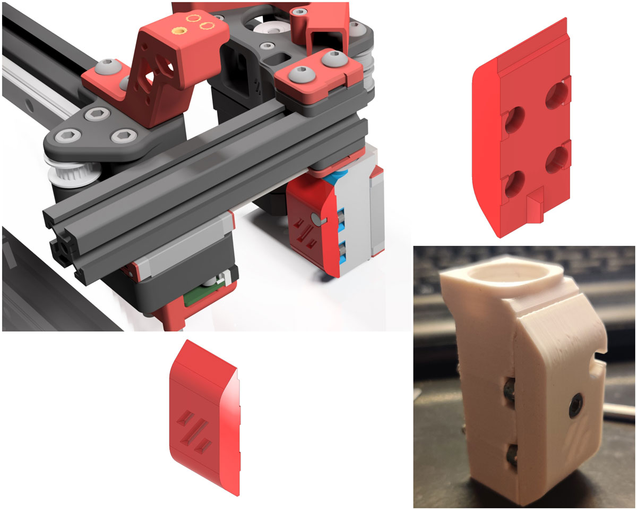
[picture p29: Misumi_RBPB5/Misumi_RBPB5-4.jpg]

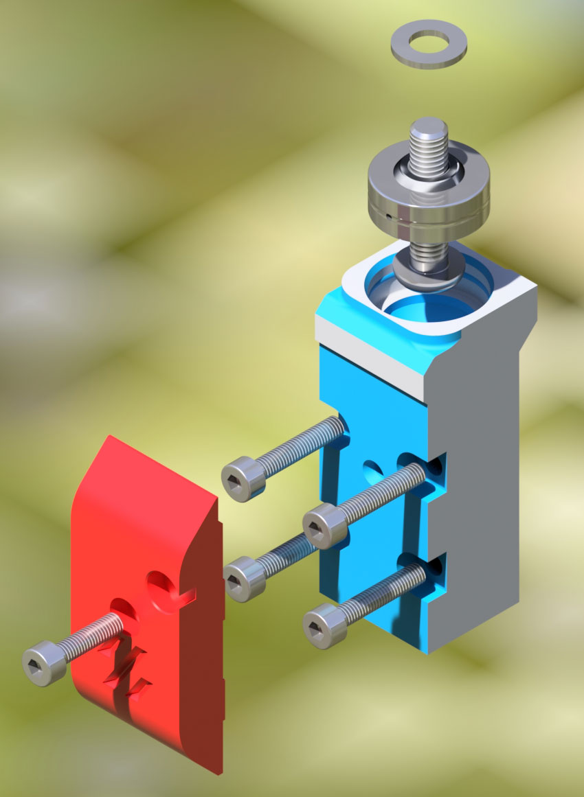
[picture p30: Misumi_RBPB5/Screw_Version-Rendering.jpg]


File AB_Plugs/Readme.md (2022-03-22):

<h1 align="center">AB Motor Plugs:</h1>
<table align="center">
  <tr>
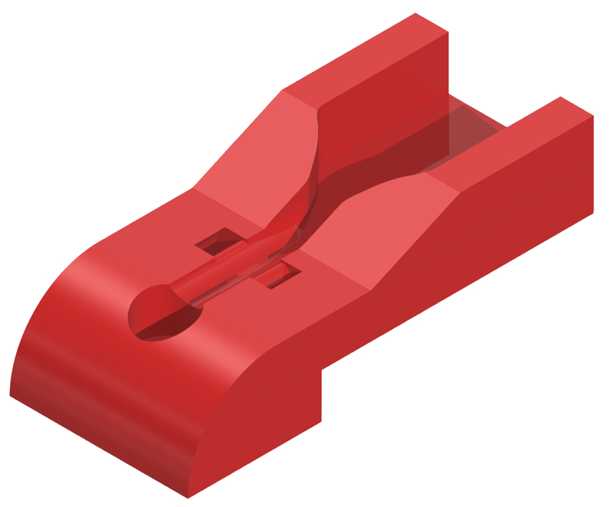
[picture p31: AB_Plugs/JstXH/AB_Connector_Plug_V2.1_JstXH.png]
    <td align="center"><a href="./JstXH">AB Plug JST-Xh<br></a></td>
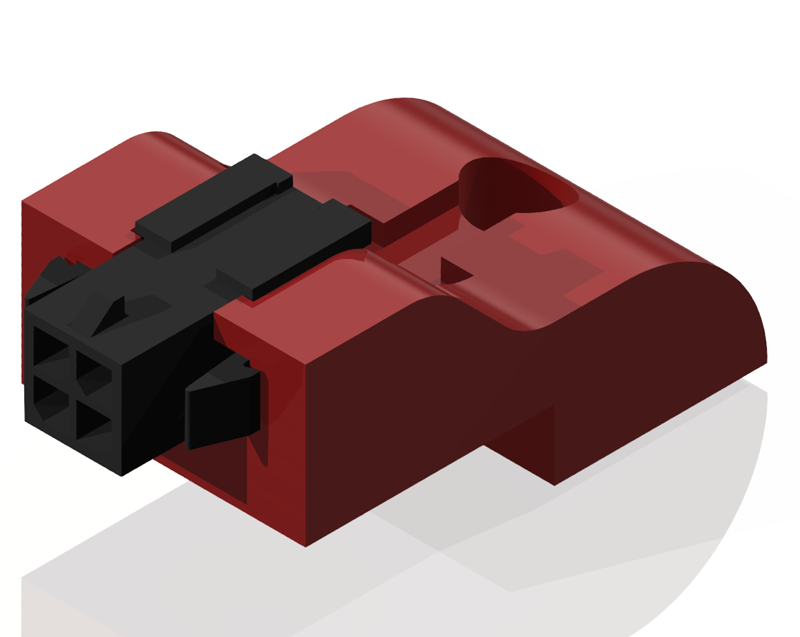
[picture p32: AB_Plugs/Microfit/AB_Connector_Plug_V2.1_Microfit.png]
    <td align="center"><a href="./Microfit">AB Plug Microfit<br></a></td>
   </tr>
</table>

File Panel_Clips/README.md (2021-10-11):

## Panel Clips
##### Credits:
- Voron Team, this is basically the same clips, just modified.

###### Printing:
- Default voron settings, correct orientation, no supports needed!

###### Bom:
- Panel Hinges: M3x40 SHCS

###### Description:
- To make it Short:
- 4mm Version = 3mm thick panels + 1mm Foam.
- 5mm Version = 3mm Panels + 2mm Foam.
- 6mm Version = 3mm Panels + 3mm Foam.
- For other versions, please ping me in Discord!

###### Description (Panel Hinges):
- Only for 3mm Panels with 12mm Wide 3M-VHB-Tape and 1mm Foam

###### Pictures:
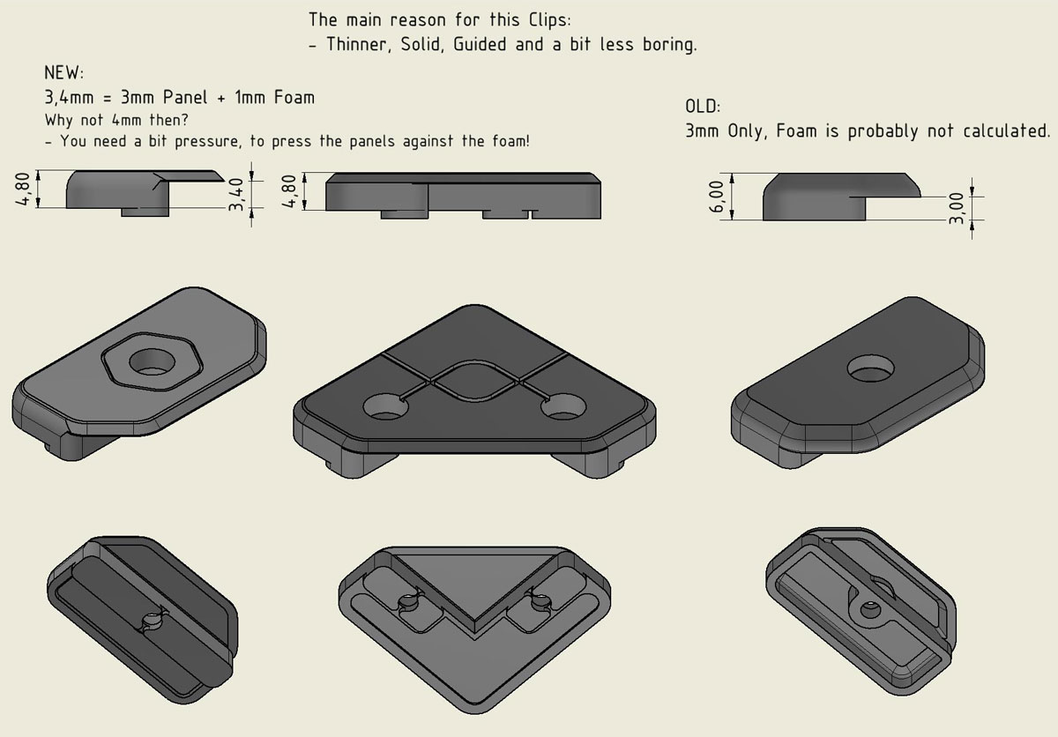
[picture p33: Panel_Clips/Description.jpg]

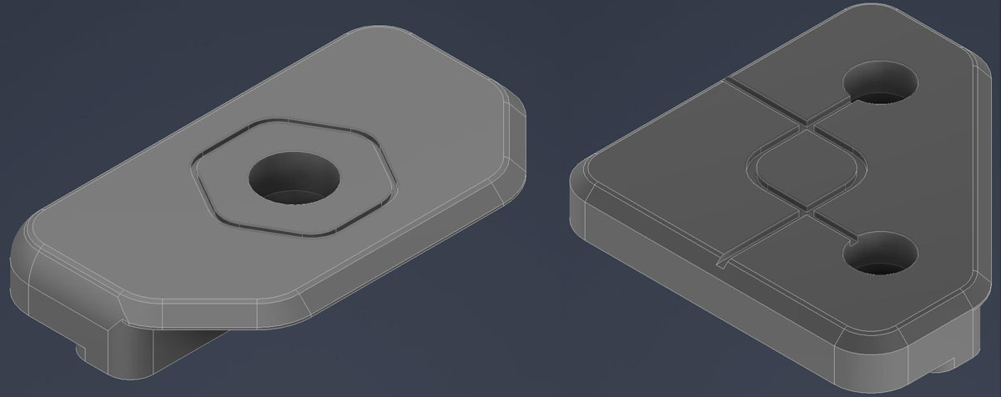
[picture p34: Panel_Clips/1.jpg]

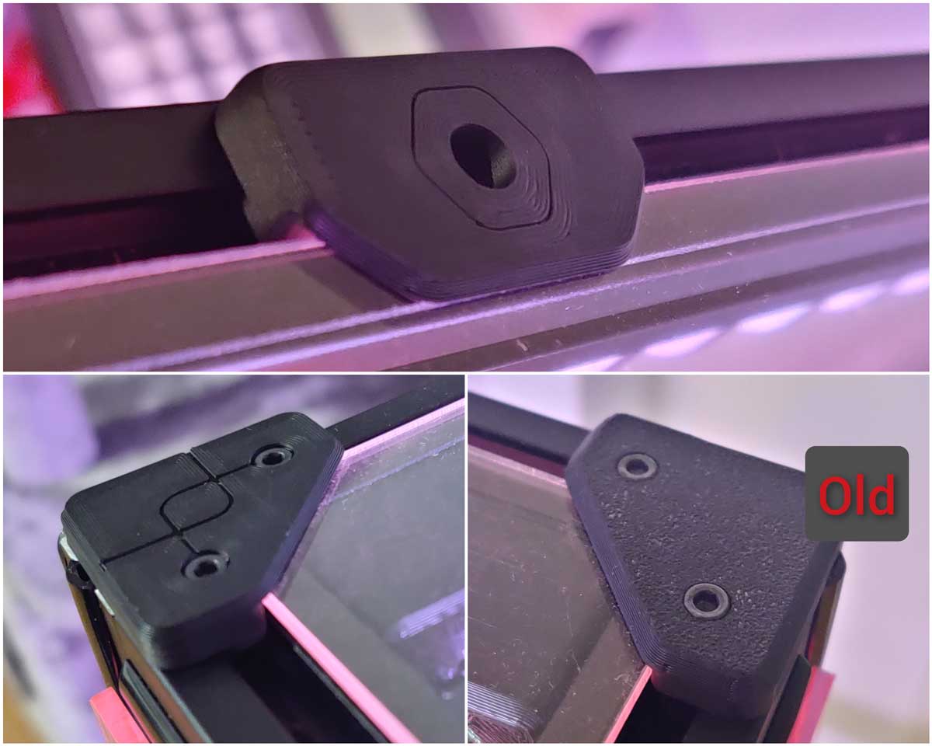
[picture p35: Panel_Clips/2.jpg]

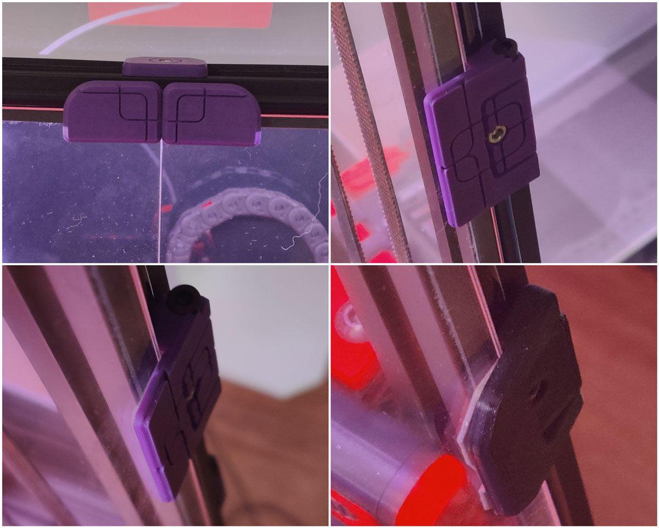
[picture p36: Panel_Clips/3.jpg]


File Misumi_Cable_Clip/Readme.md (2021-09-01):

## Misumi Cable Clip
##### Credits:
- Eddie from the Voron-Team (From his awesome Misumi Led Clips)

###### Printing:
- Default voron settings, correct orientation, no supports

###### Bom:
- Nothing

###### Description:
- It's a stupid Clip to hide your cables stiff and secure inside that extrsion cutout.
- You can scale this in Z-Size to whatever you want. By default it's 8mm, as i find it the perfect size.
- Please don't even try to print only one of this, it's tinyyy, you need layertime xD

###### Pictures:



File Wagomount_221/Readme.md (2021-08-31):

## Wago 221 DIN Mount
##### Credits:
- Voron Team :-)

###### Printing:
- Tolerances are very tight, print only with calibrated flowrate
- Default voron settings, correct orientation, no supports

###### Bom:
- 2x M2x10 Self-tapping Screw

###### Description:
- Simple design for 1/2/3 x 221 5-port wagos. I didn't found anything here that is mountable to din rails, so i made one simply.
- The wagos are sitting in there pretty extreme, so you don't need to worry about opening & closing them on the mount itself.

###### Pictures:



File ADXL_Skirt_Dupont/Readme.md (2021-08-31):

## ADXL Skirt Connector mount (Dupont Version)

##### Credits:
- @alch3my: The plug is based on his skirt insert base, which works amazing btw.

###### Printing:
- Tolerances are very tight, print only with calibrated flowrate
- Default voron settings, correct orientation, no supports

###### Bom:
- 2x m3x8 or m3x12 screws.
- 3x 3-pin Dupont
- 3x 4-pin Dupont
- 1x 8-pin Dupont (for adxl itself)
- Some cables (im using 30+20cm)

###### Description:
- Should be self explanatory in the pictures!
- The ADXL Dragon mount is available here: https://github.com/Ramalama2/Voron-2-Mods/tree/main/ADXL_Dragon_Plug

###### Pictures:


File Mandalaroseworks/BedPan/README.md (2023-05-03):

## Changelog:
Release (24.07.22): Release!
<details>
  <summary>
    Old Changelog
  </summary>
- Nothing yet.
</details>

#

## Videos:
Remove Bed: https://youtube.com/shorts/P7dfdtHAS0U<br>
Mount Bed: https://www.youtube.com/shorts/KiGKaBCcbPg<br>
Bucket: https://www.youtube.com/shorts/od5NZhmdGk4<br>

#

#

<details>
  <summary>
    CREDITS: Midnite3DP, Mandalaroseworks & all the great people we have in our community :-)<br>
  </summary>
* Midnite3DP: <a href="https://github.com/Midnite3DP/voron-bedpan">Original Bedpan</a>, Thank you very much for the Idea!!! It's basically his work just with a lot modifications, cableholder and a new bucket :-)<br>
* Mandalaroseworks: Thanks guys for making that amazing Kinematic Mount! Without you, this won't be possible!<br>
* Community: Feelingwise discord is a Place filled with only nice and always helpful People! A special thanks to all of them, i personally just love everyone there!<br>
</details>

<details>
  <summary>
    Print Settings:
  </summary>
- Default Voron settings, correct orientation, no supports needed!<br>
</details>

<details>
  <summary>
    BOM:
  </summary>
- 20x 6x3 Magnets!<br>
- 4x M3x8 SHCS - DIN 912<br>
- 6x WAGO 221-412<br>
</details>

<details>
  <summary>
    Description:
  </summary>
- Get the Power of your Kinematics mount! Easy removable and mountable bed and Bucket!<br>
- There is not much to say, watch simply the Video!<br>
- Klicky/KlickyNG/etc Compatibility! I thought about that and you can drive fully over the bucket at Z0 with klicky attached without to worry about!
</details>

## Pictures:






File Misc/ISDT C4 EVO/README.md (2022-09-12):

<h1 align="center">ISDT C4-Evo Noctua Mod</h3></p>
<br>
<details>
  <summary>
   Changelog: Release (12.09.22): ISDT C4-Evo Noctua Mod
  </summary>
- Nothing Yet! <br><br>
</details>

#
<br>
<details>
  <summary>
    Why? Because there is a version available that costs money, is shitty printable and needs supports... I can do it simply better.
  </summary>
</details>

#
<br>
<details>
  <summary>
    Print Settings:
  </summary>
- Default Voron settings, correct orientation, no supports needed!<br>
</details>

#
<br>
<details>
  <summary>
    BOM:
  </summary>
- 1x Noctua A4x10 3-Pin 5v<br>
</details>

#
<br>
<details>
  <summary>
    Description:
  </summary>
- How to open the ISDT C4?<br>
- The Answer is very easy if you know how :-)<br>
- There is a 1mm thin plastic shield glued to the screen, take a thin screwdriver put it from the side underneath and you can easy hower that screenprotector off!<br>
- 2 Screws are under the screen itself, simply rotate, the screen will fall off and you will see the screws.<br>
- The other 4 screws are easy to spot.<br>
- You don't need anything for this mod, other as an Noctua Fan! <br></details>

#

<br>
<br>


#

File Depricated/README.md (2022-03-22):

<h1 align="center">Mod Index:</h1>
<table align="center">
  <tr>
    <td align="center"><a href="./Bedhole_Plug">Bedhole Plug<br></a></td>
    <td align="center"><a href="./Exhaust_90">Exhaust 90degree<br></a></td>
  </tr>
  <tr>
    <td align="center"><a href="./Misumi_Led_Corners">Misumi Led Corners<br></a></td>
    <td align="center"><a href="./PurgeBucket_350_Klicky">Purgebucket 350 Klicky<br></a></td>
  </tr>
  <tr>
    <td align="center"><a href="./ADXL_Dragon_Plug">ADXL Dragon Plug<br></a></td>
	<td align="center"><a href="./Diverse">More Stuff<br></a></td>
  </tr>
</table>

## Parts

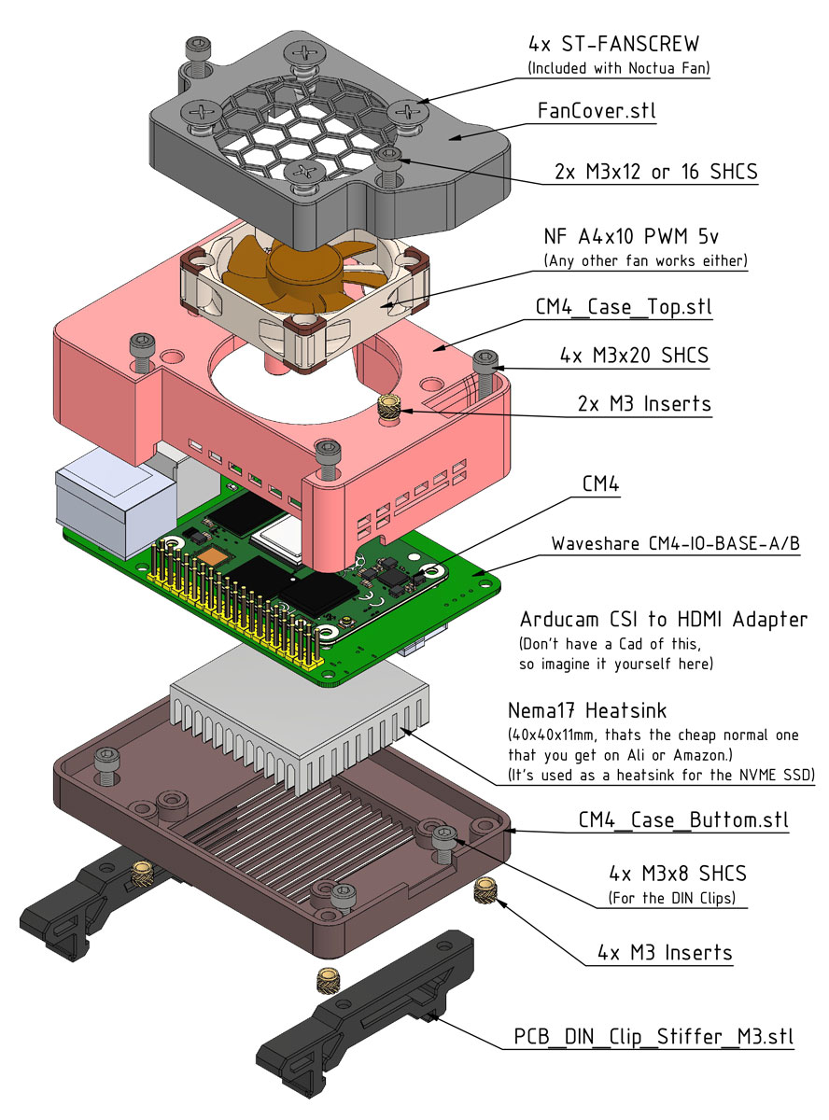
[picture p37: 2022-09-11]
Arducam_IMX477_CM4/CM4/Images/CM4_BOM.jpg

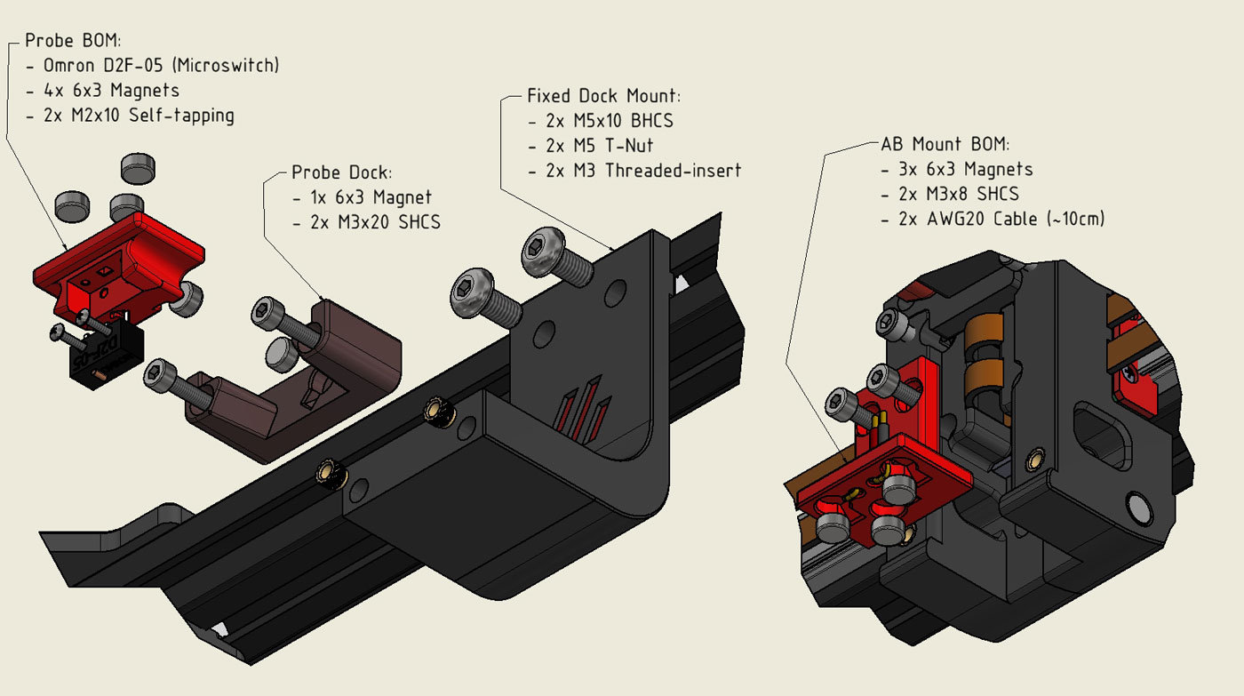
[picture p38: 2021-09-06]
Depricated/KlickyShare/BOM.jpg

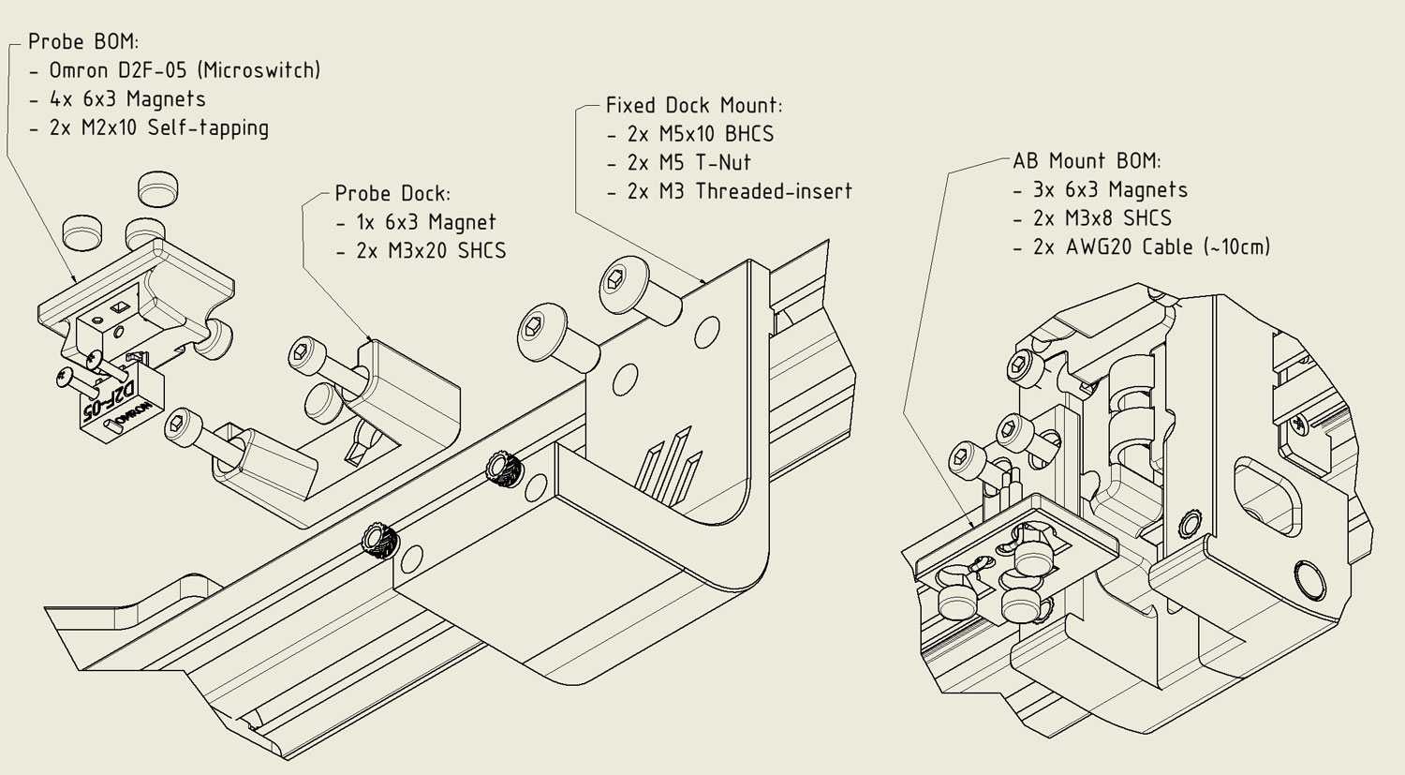
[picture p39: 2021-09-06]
Depricated/KlickyShare/BOM_SW.jpg

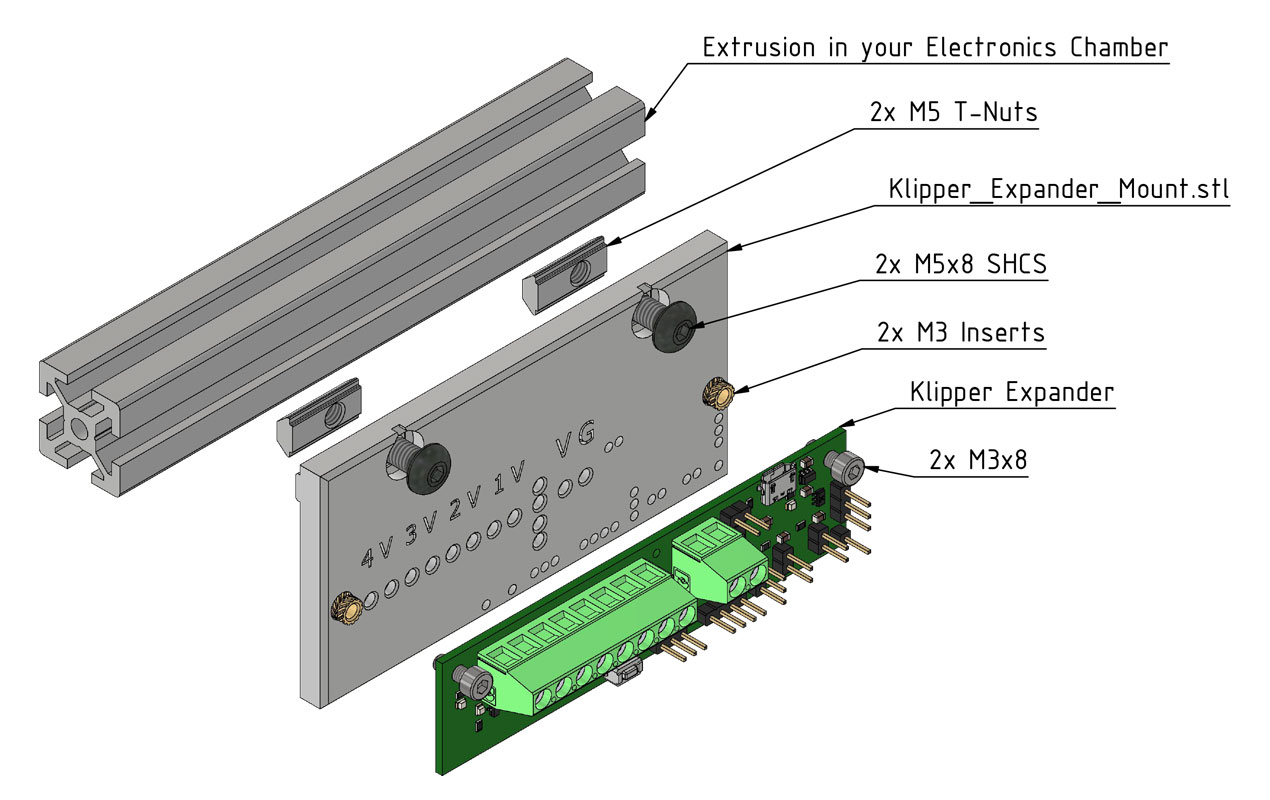
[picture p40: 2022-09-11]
Misc/Klipper_Expander_Extrusion_Mount/BOM.jpg

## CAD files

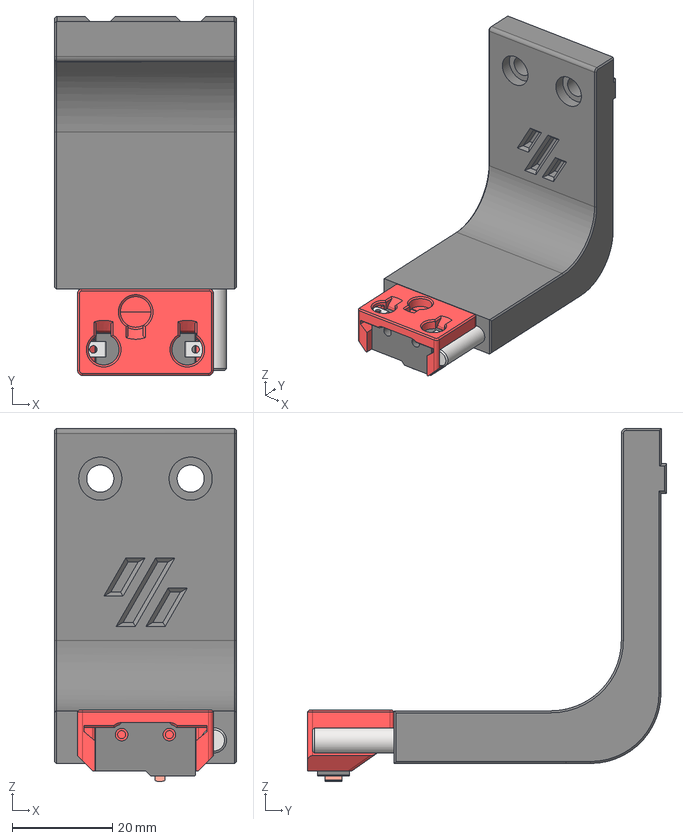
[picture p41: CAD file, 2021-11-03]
Depricated/Diverse/jlas1_Rama/CAD/Assembly.stp
36.3 x 71.5 x 70.3 mm
Glicky_3D
Bauteil17
Dock Mount fixed
Pin 5x40

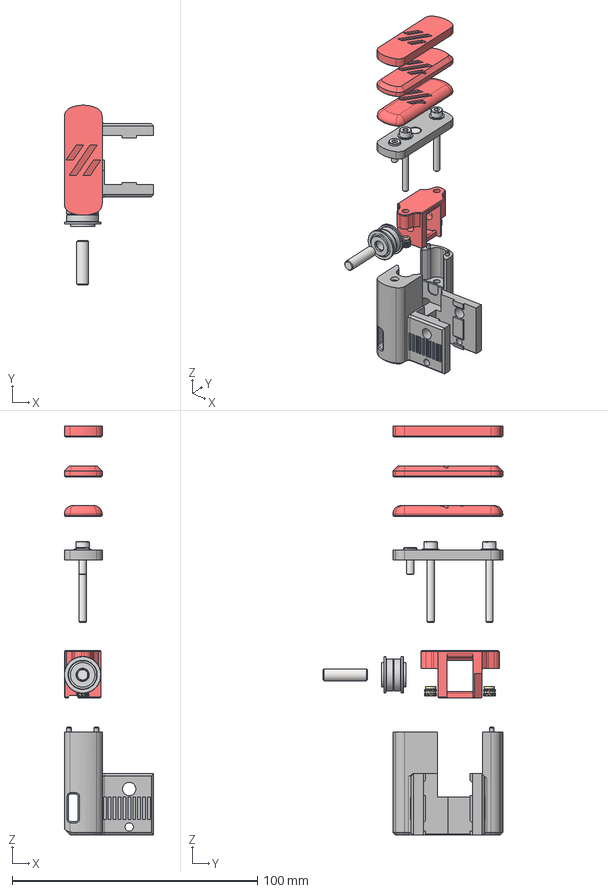
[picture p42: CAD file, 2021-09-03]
Front_Idlers/CAD/Assembly_Front-Idlers_v2.stp
36.5 x 73.2 x 166.8 mm
Front_Idler1
Cover1
Cover2
5x20 Shaft
Inside-holder
6x3 Magnet x 2
DIN 912 - M3 x 30 x 2
DIN 125 - A 3,2 x 2
DIN 912 - M3 x 8
M5 1mm Spacer (1) x 2
F695 ZZ (1) x 2
M3 Threaded Insert (1) x 2
Cover3
Cover4

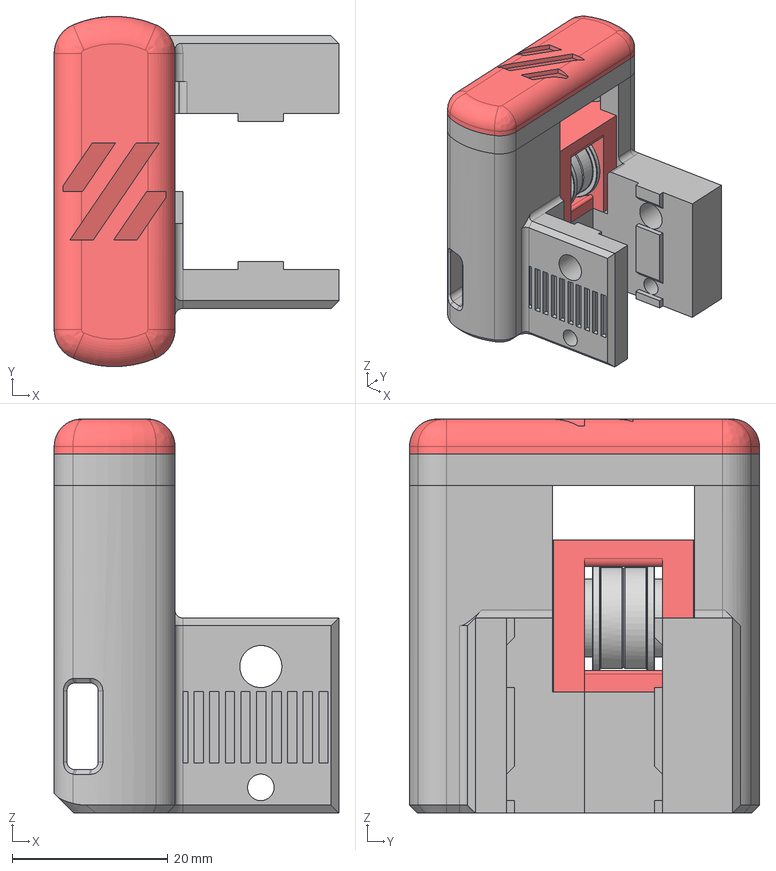
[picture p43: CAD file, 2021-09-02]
Front_Idlers/CAD/Assembly_Front-Idler-Right.stp
36.5 x 44.9 x 50.5 mm
Front_Idler1
Cover1
Cover2
5x20 Shaft
Inside-holder
6x3 Magnet x 2
DIN 912 - M3 x 30 x 2
DIN 125 - A 3,2 x 2
DIN 912 - M3 x 8
M5 1mm Spacer (1) x 2
F695 ZZ (1) x 2

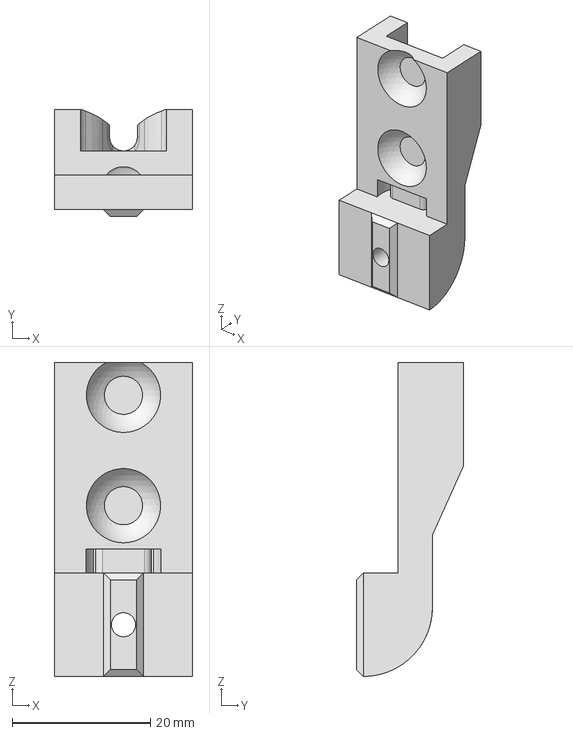
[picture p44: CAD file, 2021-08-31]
AB_Plugs/JstXH/CAD/AB_Connector_Plug_V2.1_JstXH.stp
20.0 x 15.5 x 45.5 mm

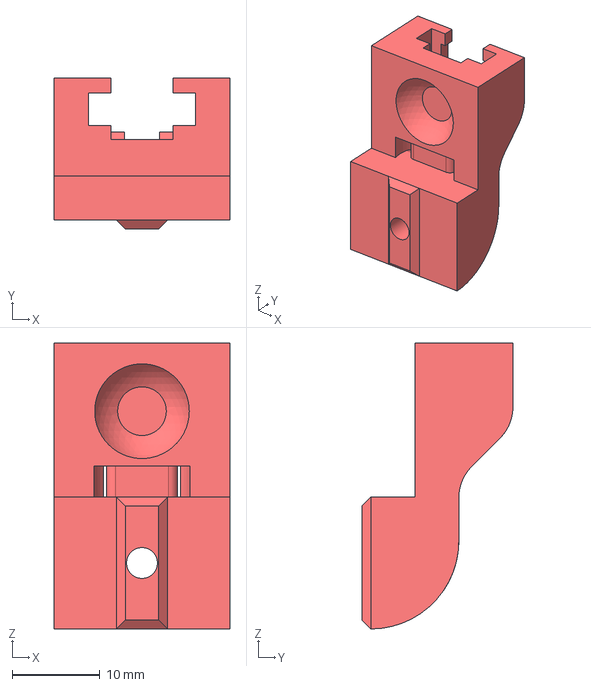
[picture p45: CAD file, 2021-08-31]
AB_Plugs/Microfit/CAD/AB_Connector_Plug_V2.1_Microfit.stp
20.0 x 17.1 x 32.5 mm

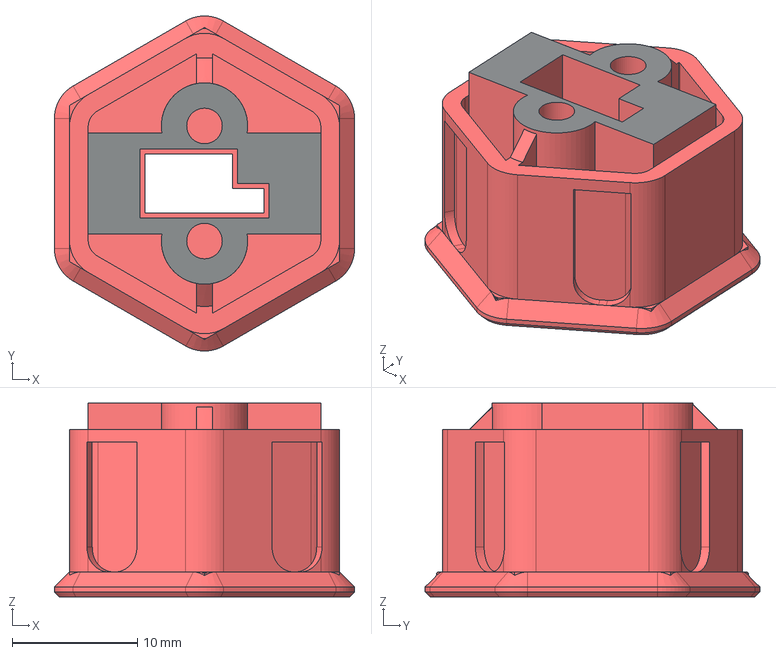
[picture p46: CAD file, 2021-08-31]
ADXL_Skirt_Dupont/CAD/ADXL_Skirt-Plug.stp
24.0 x 26.8 x 15.5 mm

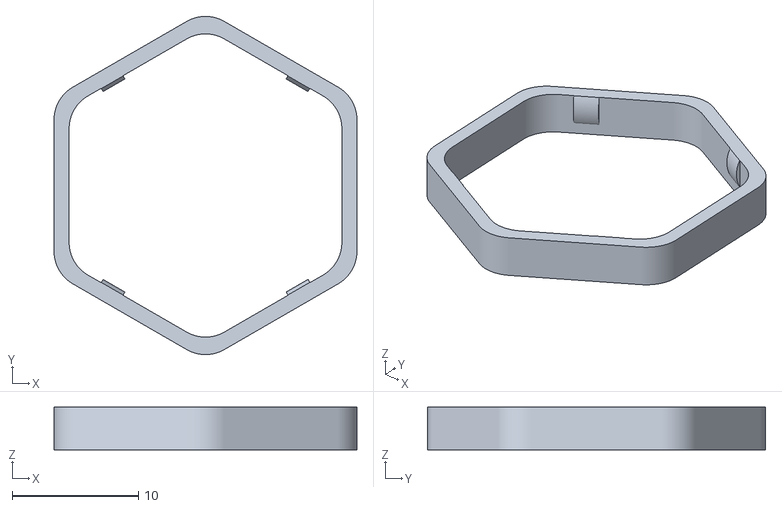
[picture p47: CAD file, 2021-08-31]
ADXL_Skirt_Dupont/STL/Lockring.stl
24.0 x 26.8 x 3.40

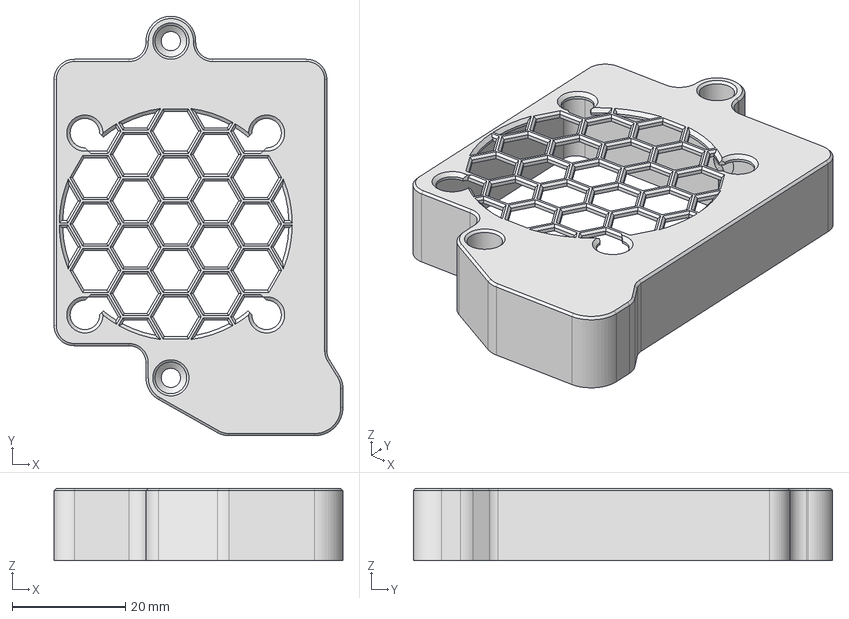
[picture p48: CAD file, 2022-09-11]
Arducam_IMX477_CM4/CM4/CAD/FanCover.stp
51.1 x 74.2 x 12.8 mm

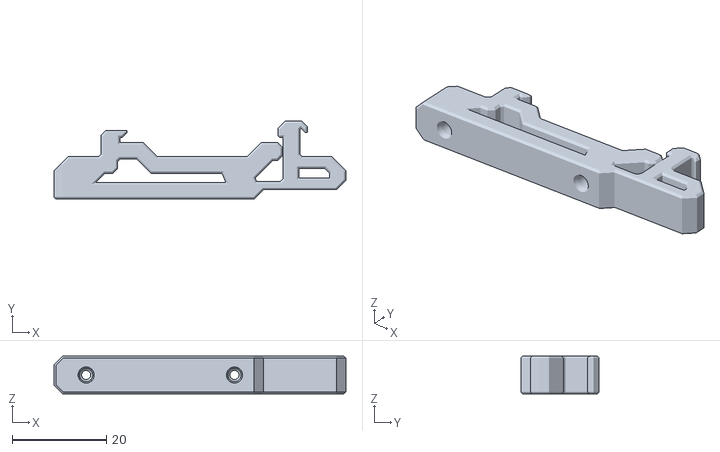
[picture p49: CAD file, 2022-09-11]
Arducam_IMX477_CM4/CM4/STL/PCB_DIN_Clip_Stiffer_M3.stl
62.0 x 16.6 x 8.00

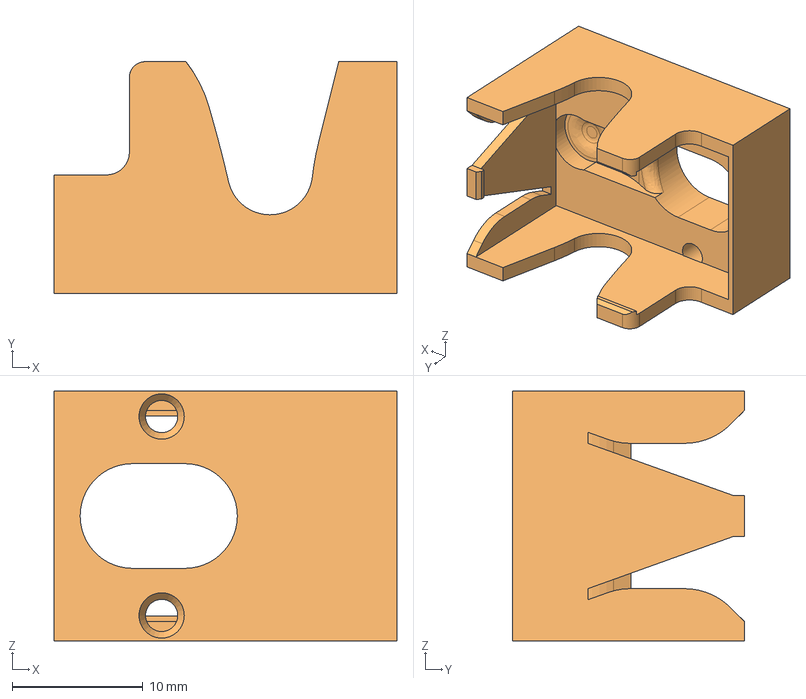
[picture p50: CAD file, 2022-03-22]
Depricated/ADXL_Dragon_Plug/CAD/Dragon_Heatblock_Plug_v2.stp
26.2 x 17.7 x 19.1 mm

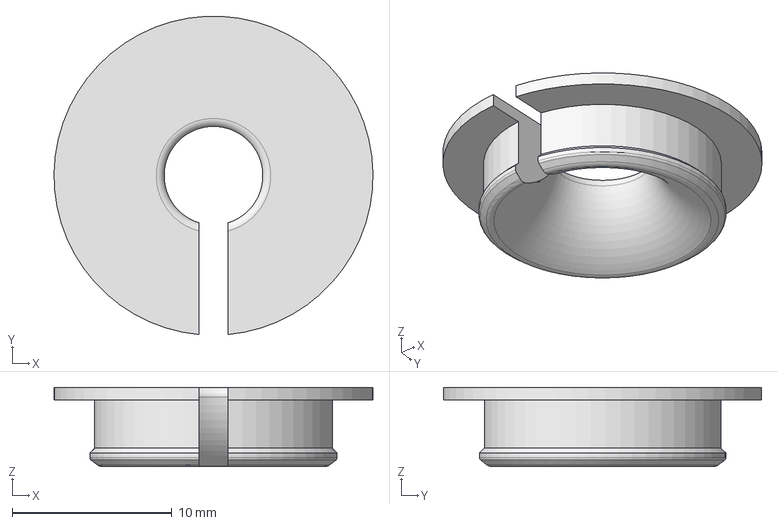
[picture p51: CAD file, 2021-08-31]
Depricated/Bedhole_Plug/CAD/Bedhole_Plug.stp
20.0 x 19.9 x 4.96 mm

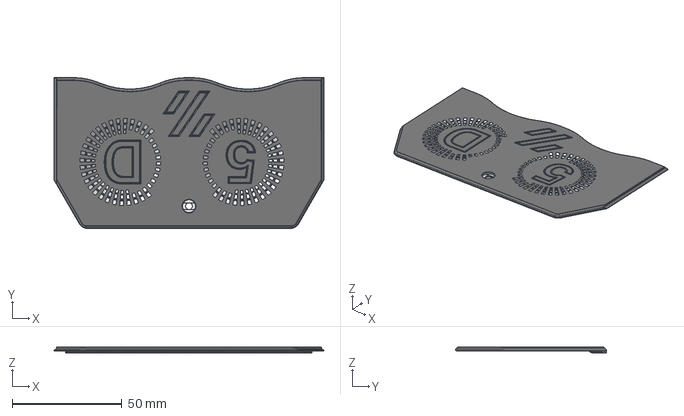
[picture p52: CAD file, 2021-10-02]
Depricated/Diverse/0ndsk4_Rama/Release_Nevermore-RLF35_LID.stp
122.8 x 68.5 x 2.80 mm

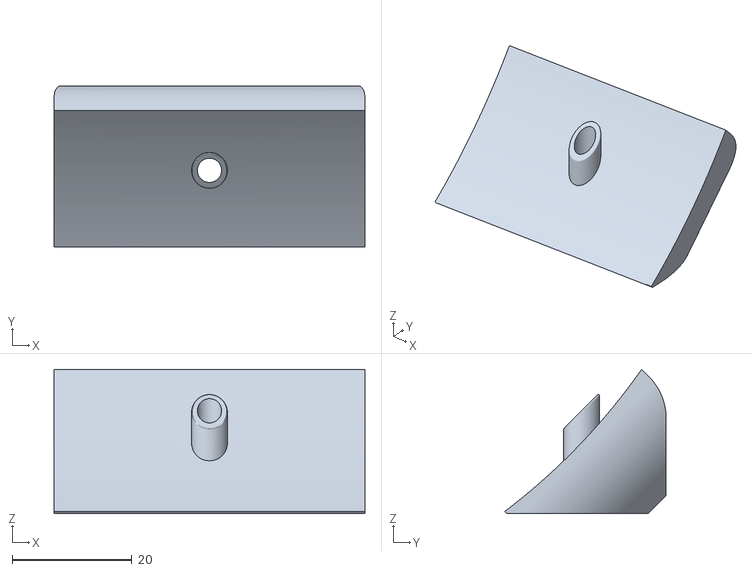
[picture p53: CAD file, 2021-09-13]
Depricated/Diverse/eSun-TopBackExit/STL/eSun_Holder.stl
52.0 x 27.0 x 24.1

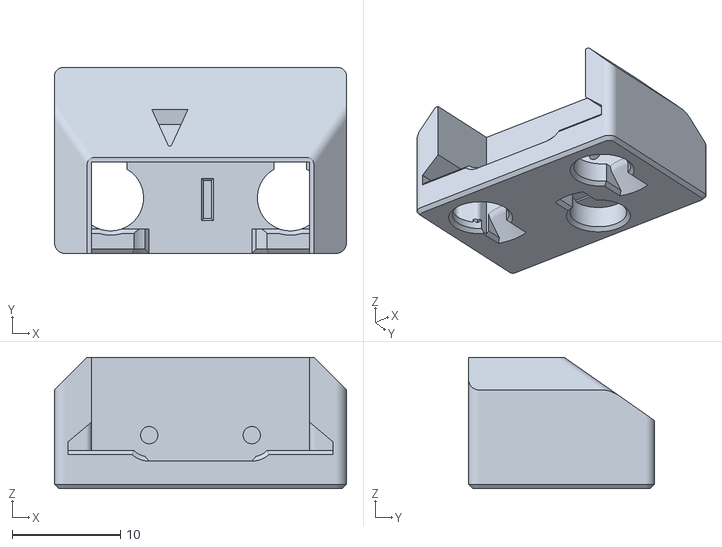
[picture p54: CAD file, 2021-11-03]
Depricated/Diverse/jlas1_Rama/STL/Probe_v1.stl
27.0 x 17.2 x 12.2

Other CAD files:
Misc/Klipper_Expander_Extrusion_Mount/CAD/Source/Assembly.dwg
Octopus_Pro_FanCase/CAD/Source/FanCase_Assembly.dwg
Arducam_IMX477_CM4/CM4/CAD/Source/CM4_BOM.dwg
Depricated/ADXL_Dragon_Plug/STL/Dragon_Clip_v2.stl
AB_Plugs/JstXH/CAD/AB_Connector_Plug_V2.1_JstXH.ipt
AB_Plugs/JstXH/STL/AB_Connector_Plug_V2.1_JstXH.stl
AB_Plugs/Microfit/CAD/AB_Connector_Plug_V2.1_Microfit.ipt
AB_Plugs/Microfit/STL/AB_Connector_Plug_V2.1_Microfit.stl
ADXL_Skirt_Dupont/CAD/ADXL_Pi-Plug.ipt
ADXL_Skirt_Dupont/CAD/ADXL_Pi-Plug.stp
ADXL_Skirt_Dupont/CAD/ADXL_Plug.ipt
ADXL_Skirt_Dupont/CAD/ADXL_Plug.stp
ADXL_Skirt_Dupont/CAD/ADXL_Skirt-Plug.ipt
ADXL_Skirt_Dupont/STL/ADXL_Pi-Plug.stl
ADXL_Skirt_Dupont/STL/ADXL_Plug.stl
ADXL_Skirt_Dupont/STL/Adxl_Skirt-Plug.stl
Arducam_IMX477_CM4/CM4/CAD/CM4_Case_Buttom.stp
Arducam_IMX477_CM4/CM4/CAD/CM4_Case_Top.stp
Arducam_IMX477_CM4/CM4/CAD/Source/CM4_Case_Buttom.ipt
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

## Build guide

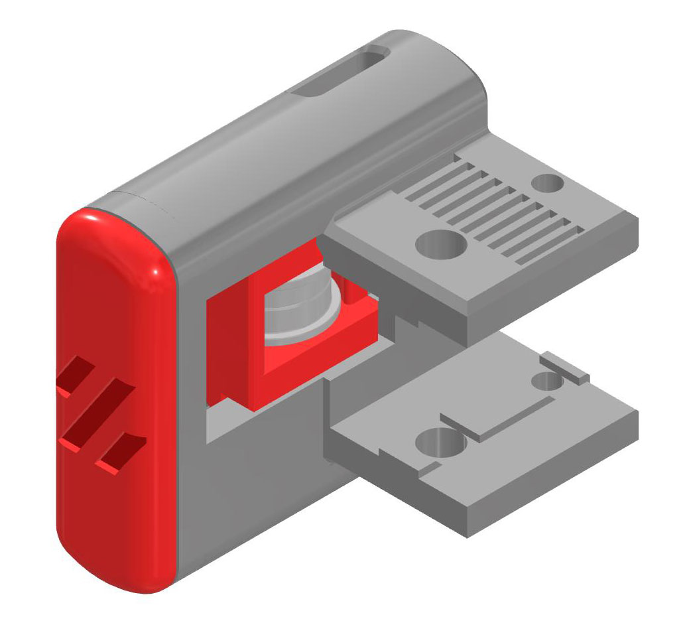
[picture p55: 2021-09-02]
Front_Idlers/Pics/Assembly_Front-Idlers55.jpg

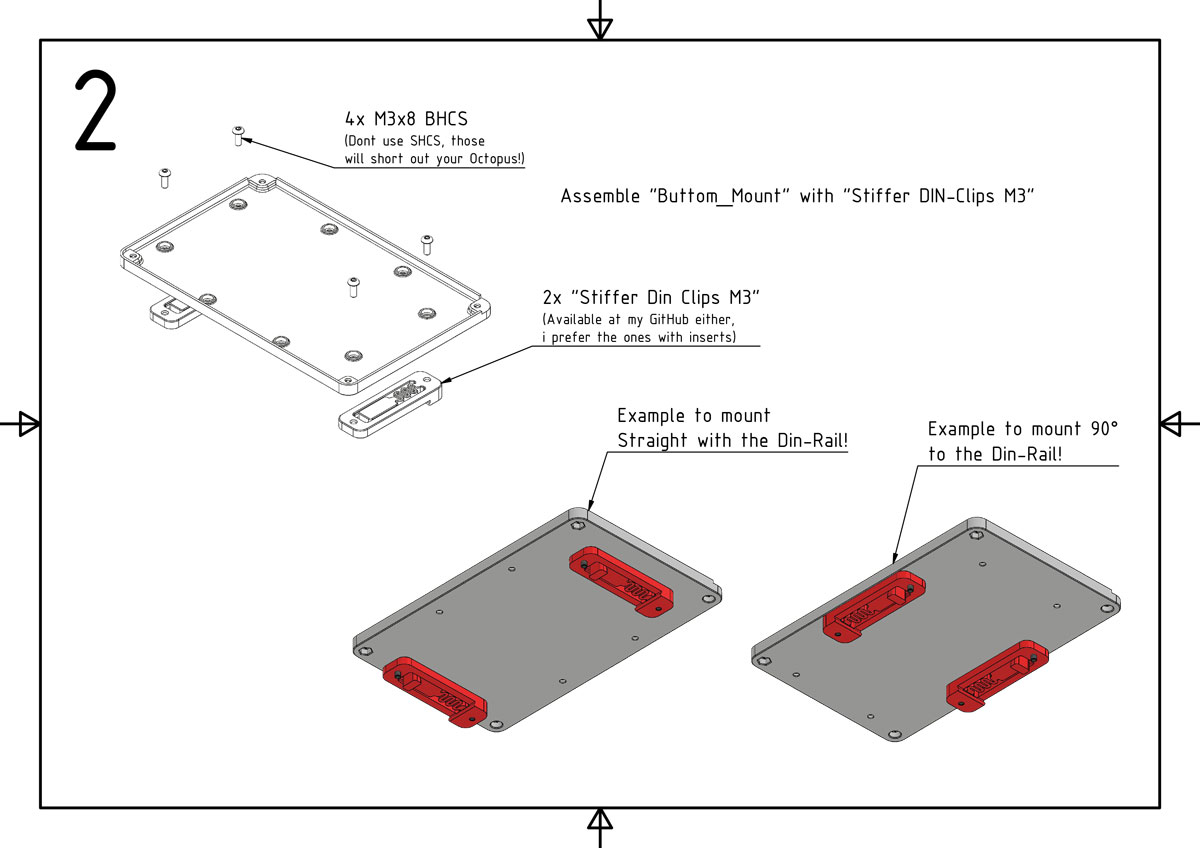
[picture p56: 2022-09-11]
Octopus_Pro_FanCase/Manual/3.jpg

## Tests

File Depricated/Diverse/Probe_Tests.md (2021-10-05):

- Command: PROBE_ACCURACY samples=20 SAMPLE_RETRACT_DIST=1 PROBE_SPEED=1
```
############# Speed: 1

- D2F-05
04:55:42 // PROBE_ACCURACY at X:175.000 Y:175.000 Z:15.000 (samples=20 retract=1.000 speed=1.0 lift_speed=8.0)
04:55:51 // probe at 175.000,175.000 is z=7.354705
04:55:53 // probe at 175.000,175.000 is z=7.357205
04:55:54 // probe at 175.000,175.000 is z=7.357205
04:55:56 // probe at 175.000,175.000 is z=7.357205
04:55:58 // probe at 175.000,175.000 is z=7.357205
04:55:59 // probe at 175.000,175.000 is z=7.357205
04:56:01 // probe at 175.000,175.000 is z=7.357205
04:56:02 // probe at 175.000,175.000 is z=7.357205
04:56:04 // probe at 175.000,175.000 is z=7.357205
04:56:05 // probe at 175.000,175.000 is z=7.357205
04:56:07 // probe at 175.000,175.000 is z=7.357205
04:56:08 // probe at 175.000,175.000 is z=7.357205
04:56:10 // probe at 175.000,175.000 is z=7.357205
04:56:11 // probe at 175.000,175.000 is z=7.357205
04:56:13 // probe at 175.000,175.000 is z=7.357205
04:56:14 // probe at 175.000,175.000 is z=7.357205
04:56:16 // probe at 175.000,175.000 is z=7.357205
04:56:17 // probe at 175.000,175.000 is z=7.357205
04:56:19 // probe at 175.000,175.000 is z=7.357205
04:56:20 // probe at 175.000,175.000 is z=7.357205
04:56:20 // probe accuracy results: maximum 7.357205, minimum 7.354705, range 0.002500, average 7.357080, median 7.357205, standard deviation 0.000545

- D2F-01
04:15:46 // PROBE_ACCURACY at X:175.000 Y:175.000 Z:15.000 (samples=20 retract=1.000 speed=1.0 lift_speed=8.0)
04:15:55 // probe at 175.000,175.000 is z=7.209705
04:15:56 // probe at 175.000,175.000 is z=7.222205
04:15:58 // probe at 175.000,175.000 is z=7.222205
04:15:59 // probe at 175.000,175.000 is z=7.222205
04:16:01 // probe at 175.000,175.000 is z=7.222205
04:16:02 // probe at 175.000,175.000 is z=7.222205
04:16:04 // probe at 175.000,175.000 is z=7.222205
04:16:05 // probe at 175.000,175.000 is z=7.224705
04:16:07 // probe at 175.000,175.000 is z=7.222205
04:16:08 // probe at 175.000,175.000 is z=7.222205
04:16:10 // probe at 175.000,175.000 is z=7.222205
04:16:11 // probe at 175.000,175.000 is z=7.222205
04:16:13 // probe at 175.000,175.000 is z=7.224705
04:16:14 // probe at 175.000,175.000 is z=7.222205
04:16:16 // probe at 175.000,175.000 is z=7.222205
04:16:17 // probe at 175.000,175.000 is z=7.224705
04:16:19 // probe at 175.000,175.000 is z=7.222205
04:16:20 // probe at 175.000,175.000 is z=7.222205
04:16:22 // probe at 175.000,175.000 is z=7.222205
04:16:23 // probe at 175.000,175.000 is z=7.224705
04:16:23 // probe accuracy results: maximum 7.224705, minimum 7.209705, range 0.015000, average 7.222080, median 7.222205, standard deviation 0.003008

- China (Red White)
05:08:34 // PROBE_ACCURACY at X:175.000 Y:175.000 Z:15.000 (samples=20 retract=1.000 speed=1.0 lift_speed=8.0)
05:08:43 // probe at 175.000,175.000 is z=7.635000
05:08:44 // probe at 175.000,175.000 is z=7.640000
05:08:46 // probe at 175.000,175.000 is z=7.642500
05:08:47 // probe at 175.000,175.000 is z=7.640000
05:08:49 // probe at 175.000,175.000 is z=7.640000
05:08:50 // probe at 175.000,175.000 is z=7.640000
05:08:52 // probe at 175.000,175.000 is z=7.640000
05:08:53 // probe at 175.000,175.000 is z=7.640000
05:08:55 // probe at 175.000,175.000 is z=7.640000
05:08:56 // probe at 175.000,175.000 is z=7.640000
05:08:58 // probe at 175.000,175.000 is z=7.640000
05:08:59 // probe at 175.000,175.000 is z=7.640000
05:09:01 // probe at 175.000,175.000 is z=7.640000
05:09:02 // probe at 175.000,175.000 is z=7.640000
05:09:04 // probe at 175.000,175.000 is z=7.640000
05:09:05 // probe at 175.000,175.000 is z=7.640000
05:09:07 // probe at 175.000,175.000 is z=7.640000
05:09:08 // probe at 175.000,175.000 is z=7.640000
05:09:10 // probe at 175.000,175.000 is z=7.640000
05:09:11 // probe at 175.000,175.000 is z=7.640000
05:09:11 // probe accuracy results: maximum 7.642500, minimum 7.635000, range 0.007500, average 7.639875, median 7.640000, standard deviation 0.001244

- Kailh-GM8
04:20:07 // PROBE_ACCURACY at X:175.000 Y:175.000 Z:15.000 (samples=20 retract=1.000 speed=1.0 lift_speed=8.0)
04:20:16 // probe at 175.000,175.000 is z=7.302205
04:20:18 // probe at 175.000,175.000 is z=7.307205
04:20:19 // probe at 175.000,175.000 is z=7.307205
04:20:21 // probe at 175.000,175.000 is z=7.307205
04:20:22 // probe at 175.000,175.000 is z=7.307205
04:20:24 // probe at 175.000,175.000 is z=7.307205
04:20:25 // probe at 175.000,175.000 is z=7.307205
04:20:27 // probe at 175.000,175.000 is z=7.307205
04:20:28 // probe at 175.000,175.000 is z=7.307205
04:20:30 // probe at 175.000,175.000 is z=7.307205
04:20:31 // probe at 175.000,175.000 is z=7.307205
04:20:33 // probe at 175.000,175.000 is z=7.307205
04:20:34 // probe at 175.000,175.000 is z=7.307205
04:20:36 // probe at 175.000,175.000 is z=7.307205
04:20:37 // probe at 175.000,175.000 is z=7.307205
04:20:39 // probe at 175.000,175.000 is z=7.307205
04:20:40 // probe at 175.000,175.000 is z=7.307205
04:20:42 // probe at 175.000,175.000 is z=7.307205
04:20:43 // probe at 175.000,175.000 is z=7.307205
04:20:45 // probe at 175.000,175.000 is z=7.307205
04:20:45 // probe accuracy results: maximum 7.307205, minimum 7.302205, range 0.005000, average 7.306955, median 7.307205, standard deviation 0.001090

############# Speed: 4

- D2F-01
05:31:07 // PROBE_ACCURACY at X:130.000 Y:298.000 Z:15.000 (samples=20 retract=1.000 speed=4.0 lift_speed=8.0)
05:31:10 // probe at 130.000,298.000 is z=7.311984
05:31:11 // probe at 130.000,298.000 is z=7.326984
05:31:12 // probe at 130.000,298.000 is z=7.326984
05:31:13 // probe at 130.000,298.000 is z=7.326984
05:31:13 // probe at 130.000,298.000 is z=7.326984
05:31:14 // probe at 130.000,298.000 is z=7.329484
05:31:15 // probe at 130.000,298.000 is z=7.326984
05:31:16 // probe at 130.000,298.000 is z=7.326984
05:31:16 // probe at 130.000,298.000 is z=7.326984
05:31:17 // probe at 130.000,298.000 is z=7.329484
05:31:18 // probe at 130.000,298.000 is z=7.329484
05:31:19 // probe at 130.000,298.000 is z=7.326984
05:31:19 // probe at 130.000,298.000 is z=7.326984
05:31:20 // probe at 130.000,298.000 is z=7.326984
05:31:21 // probe at 130.000,298.000 is z=7.326984
05:31:22 // probe at 130.000,298.000 is z=7.329484
05:31:22 // probe at 130.000,298.000 is z=7.329484
05:31:23 // probe at 130.000,298.000 is z=7.326984
05:31:24 // probe at 130.000,298.000 is z=7.326984
05:31:25 // probe at 130.000,298.000 is z=7.326984
05:31:25 // probe accuracy results: maximum 7.329484, minimum 7.311984, range 0.017500, average 7.326859, median 7.326984, standard deviation 0.003577

- China
05:26:40 // PROBE_ACCURACY at X:130.000 Y:298.000 Z:15.000 (samples=20 retract=1.000 speed=4.0 lift_speed=8.0)
05:26:43 // probe at 130.000,298.000 is z=7.606984
05:26:44 // probe at 130.000,298.000 is z=7.614484
05:26:44 // probe at 130.000,298.000 is z=7.614484
05:26:45 // probe at 130.000,298.000 is z=7.614484
05:26:46 // probe at 130.000,298.000 is z=7.614484
05:26:47 // probe at 130.000,298.000 is z=7.614484
05:26:47 // probe at 130.000,298.000 is z=7.614484
05:26:48 // probe at 130.000,298.000 is z=7.614484
05:26:49 // probe at 130.000,298.000 is z=7.616984
05:26:50 // probe at 130.000,298.000 is z=7.614484
05:26:50 // probe at 130.000,298.000 is z=7.614484
05:26:51 // probe at 130.000,298.000 is z=7.614484
05:26:52 // probe at 130.000,298.000 is z=7.614484
05:26:53 // probe at 130.000,298.000 is z=7.616984
05:26:54 // probe at 130.000,298.000 is z=7.614484
05:26:54 // probe at 130.000,298.000 is z=7.614484
05:26:55 // probe at 130.000,298.000 is z=7.614484
05:26:56 // probe at 130.000,298.000 is z=7.614484
05:26:57 // probe at 130.000,298.000 is z=7.614484
05:26:57 // probe at 130.000,298.000 is z=7.614484
05:26:57 // probe accuracy results: maximum 7.616984, minimum 7.606984, range 0.010000, average 7.614359, median 7.614484, standard deviation 0.001850

-Keilh-GM8
05:28:36 // PROBE_ACCURACY at X:130.000 Y:298.000 Z:15.000 (samples=20 retract=1.000 speed=4.0 lift_speed=8.0)
05:28:39 // probe at 130.000,298.000 is z=7.406984
05:28:40 // probe at 130.000,298.000 is z=7.411984
05:28:40 // probe at 130.000,298.000 is z=7.411984
05:28:41 // probe at 130.000,298.000 is z=7.411984
05:28:42 // probe at 130.000,298.000 is z=7.411984
05:28:43 // probe at 130.000,298.000 is z=7.411984
05:28:43 // probe at 130.000,298.000 is z=7.411984
05:28:44 // probe at 130.000,298.000 is z=7.414484
05:28:45 // probe at 130.000,298.000 is z=7.411984
05:28:46 // probe at 130.000,298.000 is z=7.411984
05:28:46 // probe at 130.000,298.000 is z=7.411984
05:28:47 // probe at 130.000,298.000 is z=7.411984
05:28:48 // probe at 130.000,298.000 is z=7.411984
05:28:49 // probe at 130.000,298.000 is z=7.414484
05:28:49 // probe at 130.000,298.000 is z=7.411984
05:28:50 // probe at 130.000,298.000 is z=7.411984
05:28:51 // probe at 130.000,298.000 is z=7.411984
05:28:52 // probe at 130.000,298.000 is z=7.411984
05:28:52 // probe at 130.000,298.000 is z=7.411984
05:28:53 // probe at 130.000,298.000 is z=7.411984
05:28:53 // probe accuracy results: maximum 7.414484, minimum 7.406984, range 0.007500, average 7.411984, median 7.411984, standard deviation 0.001369

############# Speed: 6

- D2F-01
05:32:48 // PROBE_ACCURACY at X:130.000 Y:298.000 Z:15.000 (samples=20 retract=1.000 speed=6.0 lift_speed=8.0)
05:32:50 // probe at 130.000,298.000 is z=7.306984
05:32:51 // probe at 130.000,298.000 is z=7.321984
05:32:52 // probe at 130.000,298.000 is z=7.321984
05:32:52 // probe at 130.000,298.000 is z=7.324484
05:32:53 // probe at 130.000,298.000 is z=7.324484
05:32:54 // probe at 130.000,298.000 is z=7.324484
05:32:54 // probe at 130.000,298.000 is z=7.324484
05:32:55 // probe at 130.000,298.000 is z=7.324484
05:32:56 // probe at 130.000,298.000 is z=7.324484
05:32:56 // probe at 130.000,298.000 is z=7.324484
05:32:57 // probe at 130.000,298.000 is z=7.324484
05:32:58 // probe at 130.000,298.000 is z=7.324484
05:32:58 // probe at 130.000,298.000 is z=7.324484
05:32:59 // probe at 130.000,298.000 is z=7.324484
05:33:00 // probe at 130.000,298.000 is z=7.324484
05:33:00 // probe at 130.000,298.000 is z=7.324484
05:33:01 // probe at 130.000,298.000 is z=7.324484
05:33:02 // probe at 130.000,298.000 is z=7.324484
05:33:02 // probe at 130.000,298.000 is z=7.324484
05:33:03 // probe at 130.000,298.000 is z=7.324484
05:33:03 // probe accuracy results: maximum 7.324484, minimum 7.306984, range 0.017500, average 7.323359, median 7.324484, standard deviation 0.003830

- China
05:36:37 // PROBE_ACCURACY at X:130.000 Y:298.000 Z:15.000 (samples=20 retract=1.000 speed=6.0 lift_speed=8.0)
05:36:39 // probe at 130.000,298.000 is z=7.601984
05:36:40 // probe at 130.000,298.000 is z=7.606984
05:36:40 // probe at 130.000,298.000 is z=7.606984
05:36:41 // probe at 130.000,298.000 is z=7.609484
05:36:42 // probe at 130.000,298.000 is z=7.609484
05:36:42 // probe at 130.000,298.000 is z=7.609484
05:36:43 // probe at 130.000,298.000 is z=7.609484
05:36:44 // probe at 130.000,298.000 is z=7.609484
05:36:45 // probe at 130.000,298.000 is z=7.609484
05:36:45 // probe at 130.000,298.000 is z=7.609484
05:36:46 // probe at 130.000,298.000 is z=7.609484
05:36:47 // probe at 130.000,298.000 is z=7.609484
05:36:47 // probe at 130.000,298.000 is z=7.609484
05:36:48 // probe at 130.000,298.000 is z=7.606984
05:36:49 // probe at 130.000,298.000 is z=7.609484
05:36:49 // probe at 130.000,298.000 is z=7.606984
05:36:50 // probe at 130.000,298.000 is z=7.606984
05:36:51 // probe at 130.000,298.000 is z=7.609484
05:36:51 // probe at 130.000,298.000 is z=7.609484
05:36:52 // probe at 130.000,298.000 is z=7.609484
05:36:52 // probe accuracy results: maximum 7.609484, minimum 7.601984, range 0.007500, average 7.608484, median 7.609484, standard deviation 0.001837

-Keilh-GM8
05:38:32 // PROBE_ACCURACY at X:130.000 Y:298.000 Z:15.000 (samples=20 retract=1.000 speed=6.0 lift_speed=8.0)
05:38:34 // probe at 130.000,298.000 is z=7.399484
05:38:35 // probe at 130.000,298.000 is z=7.404484
05:38:35 // probe at 130.000,298.000 is z=7.406984
05:38:36 // probe at 130.000,298.000 is z=7.406984
05:38:37 // probe at 130.000,298.000 is z=7.406984
05:38:37 // probe at 130.000,298.000 is z=7.406984
05:38:38 // probe at 130.000,298.000 is z=7.406984
05:38:39 // probe at 130.000,298.000 is z=7.406984
05:38:39 // probe at 130.000,298.000 is z=7.406984
05:38:40 // probe at 130.000,298.000 is z=7.406984
05:38:41 // probe at 130.000,298.000 is z=7.406984
05:38:41 // probe at 130.000,298.000 is z=7.406984
05:38:42 // probe at 130.000,298.000 is z=7.406984
05:38:43 // probe at 130.000,298.000 is z=7.406984
05:38:43 // probe at 130.000,298.000 is z=7.406984
05:38:44 // probe at 130.000,298.000 is z=7.406984
05:38:45 // probe at 130.000,298.000 is z=7.406984
05:38:45 // probe at 130.000,298.000 is z=7.406984
05:38:46 // probe at 130.000,298.000 is z=7.406984
05:38:47 // probe at 130.000,298.000 is z=7.406984
05:38:47 // probe accuracy results: maximum 7.406984, minimum 7.399484, range 0.007500, average 7.406484, median 7.406984, standard deviation 0.001696

############# Speed: 8

- D2F-01
05:33:45 // PROBE_ACCURACY at X:130.000 Y:298.000 Z:15.000 (samples=20 retract=1.000 speed=8.0 lift_speed=8.0)
05:33:47 // probe at 130.000,298.000 is z=7.306984
05:33:47 // probe at 130.000,298.000 is z=7.319484
05:33:48 // probe at 130.000,298.000 is z=7.321984
05:33:48 // probe at 130.000,298.000 is z=7.321984
05:33:49 // probe at 130.000,298.000 is z=7.321984
05:33:50 // probe at 130.000,298.000 is z=7.321984
05:33:50 // probe at 130.000,298.000 is z=7.321984
05:33:51 // probe at 130.000,298.000 is z=7.321984
05:33:52 // probe at 130.000,298.000 is z=7.321984
05:33:52 // probe at 130.000,298.000 is z=7.321984
05:33:53 // probe at 130.000,298.000 is z=7.321984
05:33:54 // probe at 130.000,298.000 is z=7.321984
05:33:54 // probe at 130.000,298.000 is z=7.321984
05:33:55 // probe at 130.000,298.000 is z=7.321984
05:33:55 // probe at 130.000,298.000 is z=7.321984
05:33:56 // probe at 130.000,298.000 is z=7.321984
05:33:57 // probe at 130.000,298.000 is z=7.321984
05:33:57 // probe at 130.000,298.000 is z=7.321984
05:33:58 // probe at 130.000,298.000 is z=7.321984
05:33:59 // probe at 130.000,298.000 is z=7.321984
05:33:59 // probe accuracy results: maximum 7.321984, minimum 7.306984, range 0.015000, average 7.321109, median 7.321984, standard deviation 0.003286

- China
05:36:07 // PROBE_ACCURACY at X:130.000 Y:298.000 Z:15.000 (samples=20 retract=1.000 speed=8.0 lift_speed=8.0)
05:36:09 // probe at 130.000,298.000 is z=7.596984
05:36:09 // probe at 130.000,298.000 is z=7.604484
05:36:10 // probe at 130.000,298.000 is z=7.604484
05:36:11 // probe at 130.000,298.000 is z=7.606984
05:36:11 // probe at 130.000,298.000 is z=7.606984
05:36:12 // probe at 130.000,298.000 is z=7.604484
05:36:12 // probe at 130.000,298.000 is z=7.604484
05:36:13 // probe at 130.000,298.000 is z=7.604484
05:36:14 // probe at 130.000,298.000 is z=7.604484
05:36:14 // probe at 130.000,298.000 is z=7.601984
05:36:15 // probe at 130.000,298.000 is z=7.604484
05:36:16 // probe at 130.000,298.000 is z=7.604484
05:36:16 // probe at 130.000,298.000 is z=7.604484
05:36:17 // probe at 130.000,298.000 is z=7.604484
05:36:18 // probe at 130.000,298.000 is z=7.604484
05:36:18 // probe at 130.000,298.000 is z=7.604484
05:36:19 // probe at 130.000,298.000 is z=7.604484
05:36:20 // probe at 130.000,298.000 is z=7.601984
05:36:20 // probe at 130.000,298.000 is z=7.604484
05:36:21 // probe at 130.000,298.000 is z=7.604484
05:36:21 // probe accuracy results: maximum 7.606984, minimum 7.596984, range 0.010000, average 7.604109, median 7.604484, standard deviation 0.001980

-Keilh-GM8
05:39:08 // PROBE_ACCURACY at X:130.000 Y:298.000 Z:15.000 (samples=20 retract=1.000 speed=8.0 lift_speed=8.0)
05:39:10 // probe at 130.000,298.000 is z=7.394484
05:39:10 // probe at 130.000,298.000 is z=7.401984
05:39:11 // probe at 130.000,298.000 is z=7.399484
05:39:12 // probe at 130.000,298.000 is z=7.401984
05:39:12 // probe at 130.000,298.000 is z=7.401984
05:39:13 // probe at 130.000,298.000 is z=7.401984
05:39:14 // probe at 130.000,298.000 is z=7.401984
05:39:14 // probe at 130.000,298.000 is z=7.401984
05:39:15 // probe at 130.000,298.000 is z=7.401984
05:39:16 // probe at 130.000,298.000 is z=7.401984
05:39:16 // probe at 130.000,298.000 is z=7.401984
05:39:17 // probe at 130.000,298.000 is z=7.401984
05:39:18 // probe at 130.000,298.000 is z=7.401984
05:39:18 // probe at 130.000,298.000 is z=7.401984
05:39:19 // probe at 130.000,298.000 is z=7.401984
05:39:19 // probe at 130.000,298.000 is z=7.401984
05:39:20 // probe at 130.000,298.000 is z=7.401984
05:39:21 // probe at 130.000,298.000 is z=7.401984
05:39:21 // probe at 130.000,298.000 is z=7.401984
05:39:22 // probe at 130.000,298.000 is z=7.401984
05:39:22 // probe accuracy results: maximum 7.401984, minimum 7.394484, range 0.007500, average 7.401484, median 7.401984, standard deviation 0.001696
```

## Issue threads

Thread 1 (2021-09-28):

Hi

tomaszeman, 2021-09-28:
Thank you for mention. Will test your version btw. I already added version that fits both e3d and dragon but it's little less stiffer than the original one. (i think your version will fit to e3d too)

Ramalama2, 2021-09-28:
I seen your new version, actually i like it, just need to print it with 99.8% dimensions 😬
Then it sits better.

Actually the difference between your version and mine is simple...
Mine sits super tight on the heatblock and no wiggling, but is a pain in the a... to mount and unmount...
Yours with 99.8% dimensions, is super nice to mount/unmount, but feels like it isn't super tight on the block ....

I wish we could combine only the positive sides of our both designs 🤦😂

Ramalama2, 2021-11-09:
Closed

Closed 2021-11-09.

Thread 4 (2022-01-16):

Locator pins are a little fragile and easily broken

nigelpjames, 2022-01-16:
Ive printed a few of these now and always manage to break off the top locator pins at the unsecured end.  Would be helpful if you could revise these to make them a little more robust

nigelpjames, 2022-01-16:
I modified the base and changed the pins to holes I can use short metal pins to locate the tensioner end cap.  No more broken pins for me ;-)

Ramalama2, 2022-02-06:
Not everyone has metal short pins 🙈
But i will think how to improve that

mvdveer, 2022-06-17:
Had the same issue - just enlarged the locating holes on the cover

nigelpjames, 2022-12-13:
Finally got around to testing nipplefix....works really well - case closed :-)

Closed 2023-05-03.

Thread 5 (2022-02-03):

mgn9 extrusion backers compatible?

Papa-Oso, 2022-02-03:
Hi, great mod! Thanks! Are these compatible with MGN9 extrusion backers?

Ramalama2, 2022-02-06:
Hi, which mod?

Ramalama2, 2022-03-23:
> https://github.com/VoronDesign/VoronUsers/tree/master/printer_mods/bythorsthunder/MGN9_Backers
> […](#)
> On Sun, Feb 6, 2022 at 5:48 PM Ramalama2 ***@***.***> wrote: Hi, which mod? — Reply to this email directly, view it on GitHub <[#5 (comment)](https://github.com/Ramalama2/Voron-2-Mods/issues/5#issuecomment-1030943062)>, or unsubscribe <https://github.com/notifications/unsubscribe-auth/AXSZX267IMYYDE2E522CS73UZ4CDDANCNFSM5NPNIN5A> . Triage notifications on the go with GitHub Mobile for iOS <https://apps.apple.com/app/apple-store/id1477376905?ct=notification-email&mt=8&pt=524675> or Android <https://play.google.com/store/apps/details?id=com.github.android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>. You are receiving this because you authored the thread.Message ID: ***@***.***>

You mean the Front Idlers?
-> if yes, then yes, fully!

Im going to Close this, Cheers :-)

Closed 2022-03-23.

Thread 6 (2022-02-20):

Trident Front idlers

TadasMit, 2022-02-20:
Hi. I made a mod for your front idlers to better fit the Trident. Are you interested in posting in your rep? If so, let me know how to send the files to you.
I have printed, assembled the new idlers fits well, works well :)

Thanx!

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

Ramalama2, 2022-02-20:
Awesome, the only problem is, that you catched me in my holidays 🙈If you have discord you can write me there Rama#6392, if not just make a pull request.Thanks for the work 👍😂Am 20.02.2022 02:06 schrieb TadasMit ***@***.***>:
Hi. I made a mod for your front idlers to better fit the Trident. Are you interested in posting in your rep? If so, let me know how to send the files to you.
I have printed, assembled the new idlers fits well, works well :)
Thanx!

—Reply to this email directly, view it on GitHub, or unsubscribe.Triage notifications on the go with GitHub Mobile for iOS or Android.
You are receiving this because you are subscribed to this thread.Message ID: ***@***.***>

aksqlt, 2022-03-12:
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

Hi TadasMit
would you mind to share your stl files with me? I'm building Trident and made similar modifications but forgot about door
 clearance :(
 thanks
 -Alex

TadasMit, 2022-03-13:
[Front Idlers.zip](https://github.com/Ramalama2/Voron-2-Mods/files/8240587/Front.Idlers.zip)
Hi Alex,

I am attaching zip files for Front Idlers (Trident mod). I also sent files to Rama; hopefully, he will have time to put them on his Github :)

aksqlt, 2022-03-14:
> [Front Idlers.zip](https://github.com/Ramalama2/Voron-2-Mods/files/8240587/Front.Idlers.zip) Hi Alex,
>
> I am attaching zip files for Front Idlers (Trident mod). I also sent files to Rama; hopefully, he will have time to put them on his Github :)

Thank you!!!

Ramalama2, 2022-03-23:
@TadasMit Idlers are merged now. So im going to Close this issue :-)

Note: The Repo was updated and no one needs to reprint the Trident Idlers, if you are using Tadas Version already from above!
Everyone else that use 2.4 Idlers on Trident, should switch.

Thanks again @TadasMit and everyone else!

Closed 2022-03-23.

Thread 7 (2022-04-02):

5M 22mm  available at MacMaster-Carr

NikosSprocket, 2022-04-02:
Not really an issue just an FYI.

MacMaster-Carr carries 5M 22mm 18-8 Stainless Steel Button Head Hex Drive Screws for $11.00 pack of 100.
Can be found at this [link](https://www.mcmaster.com/92095A482).

Also, M5 washers DIN 433 18-8 Stainless Steel from MacMaster-Carr at [link](https://www.mcmaster.com/98689A114) for $3.71 pack of 100.

Also, I have used your latest STEP files (awesome! Thank You!) and assembled them in Fusion360. I have put some samples:
[Pic1](https://bricksafe.com/files/NikosSprocket/fusion-360/2022-04-02_00h48_07.png/1280x1512.png)
[Pic2](https://bricksafe.com/files/NikosSprocket/fusion-360/2022-04-02_00h51_32.png/1280x1600.png)
[Pic3](https://bricksafe.com/files/NikosSprocket/fusion-360/2022-04-02_00h52_54.png/1280x1755.png)

Late me know if you would like some larger or you can use these.

Cheers!

Ramalama2, 2022-04-02:
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

Hey Niko, thanks for the hint. I will add the info and your Fusion Pics to the Repo.
Just if possible, could you share your fusion sources either, so i wont get penetrated so often, that i release only inventor files and no fusion files :-( (Sadly im working only with inventor and not fusion) xD

NikosSprocket, 2022-04-02:
Hi!

Of course; the only problem is that I am new to GitHub and I not familiar with uploading files etc. I have an account and familiar with unix svn but new to GitHub. Can you tell me how to upload the Fusion360 file?

btw, the MiSUMi RBPB5 is press fitted to the Z-Joint and the build in groove in the Z-joint is sufficient to hold the bearing from moving up/down?

Cheers!
Nikos

Ramalama2, 2022-07-03:
A bit late but:
For 1. you can simply send me over discord, thats the easy way, or make a pull request, for that you need to fork the repo etc 🙈

For 2. let's hope that picture is self explaining. An ender 3 weights for sure a lot more as a gantry 🙈
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

Closed 2023-05-03.

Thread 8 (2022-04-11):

Rename STLs to show x2 and accent color

rlaferla, 2022-04-11:
Please rename Trident and 2.4 STLs to show x2 and accent color in the filename.

i.e.  [a]_ for accent color and _x2.stl for print two of these.

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

Ramalama2, 2023-05-03:
I don't see any point in that, sorry :-)

I mean its basically always only 3-4 Stls, and in general very small mods. Not a big project where you can loose overview :-)
But thx & Cheers :-)

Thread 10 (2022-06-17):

Part orientation when installing

mvdveer, 2022-06-17:
Doing a new 2.4r2 build. Some observations: Printed really well - followed instructions on Github re assembly - no issues at all. When installing the idlers on Y on a new build, following the manual, it may be confusing for newbies as the original idlers have 2 x 5mm holes on the top and a 5mm and 3 mm on the bottom, which allows for easy orientation (as per the manual). This mod has a 5mm and 3mm on both top and bottom and pully orientation may be tricky. As it is still in Beta, this may be something to consider.

Ramalama2, 2022-07-03:
Hi, on the voron 2.4, there is no need for any orientation, since you can mount them only "correct". It's the same housing for left/right.

On the Trident, i made a small hole thingy on the bottom, so that you "know" the orientation. Just don't remember if i mentioned it somewhere 🙈

The holes are intented to be same on top/bottom.
There are 2 reasons for that.
1. Some people use linear rails at the top as backers, with 2xM5 holes they won't fit.
2. On the 2.4 you don't need 2 different housings (you would need if the top had different holes as the bottom), that means additionally that you aren't able to mount them wrong.

Sry, im a bit late with replying, feel free to close the issue if it's solved 😂
Cheers

mvdveer, 2022-07-03:
Thanks for the clarification, fully understand your rationale.  I fitted them without a problem, was just an observation relating to the manual .

Great mod.

Hope to see it in the next Voron 2.4 release.

Closed 2022-07-03.

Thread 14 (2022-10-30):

GE5C version

EricZimmerman, 2022-10-30:
Are the left and right portions of these:

https://github.com/Ramalama2/Voron-2-Mods/tree/main/Front_Idlers/Voron%202.4/STL/Alternatives/GE5C_Version

going to work with the default inlets:

https://github.com/Ramalama2/Voron-2-Mods/blob/main/Front_Idlers/Voron%202.4/STL/Front-Idlers_Inlet-5.15mm_default.stl

the description says to simply print things 2x, but the GE5Cs mention a left and right. why is that?

just want to make sure i have what i need before install.

thanks!

EricZimmerman, 2022-11-08:
Nothing on this? The parts can really use a good round of documentation as to what works for what and why you would want different things.

blownupp, 2023-05-02:
I’d like to second this - for the life of me I can’t tell the difference between the L and R pieces

Closed 2023-05-03.

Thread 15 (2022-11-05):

Nipple Fix for trident version

chris155hp, 2022-11-05:
please add the trident version with the nipple fix change =) thanks

pheonix3330, 2023-03-11:
@chris155hp You probably don't need these anymore, but i'll link my modified files here in case anyone is looking for it later.

I have been using it on my trident and they work great.

[Front-Idlers_Housing_Trident_Nipple-Fix.zip](https://github.com/Ramalama2/Voron-2-Mods/files/10948885/Front-Idlers_Housing_Trident_Nipple-Fix.zip)

Ramalama2, 2023-05-03:
Thanks phoenix!

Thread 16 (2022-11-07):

Confused by text on image :-)

Jaans, 2022-11-07:
Thank you for the LGX lite mod!!

I'm looking at this image from it and I'm somewhat confused:
https://github.com/Ramalama2/Voron-2-Mods/blob/main/SB_LGXlitePCB/Images/3.jpg

Is the text meant to be swapped with the other image? Did you not mean that your new PCB is the better solution?
Or am I completely misunderstanding something here?

Thanks for your time and sharing this mod

cjackson234, 2022-11-19:
I think he's saying directly soldering the wires to the board isn't the best way to do it. However, it is the most compact.

Ramalama2, 2023-05-03:
> I think he's saying directly soldering the wires to the board isn't the best way to do it. However, it is the most compact.

Exactly that xD

And yes the Pic is bad choosen afterwards :-)

Closed 2023-05-03.

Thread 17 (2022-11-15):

LGX Lite for ERCF filament sensor

Jaans, 2022-11-15:
Hi Rama,

Thank you for the amazing work you guys have been doing with this.

Are there any plans to make the same modifications to the ERCF version of the LGX Lite model from Eytecz?

Alternatively, are you able to describe the relevant changes you've made?
That way I can try to repeat them myself on the ERCF version from Eytecz's models.

Thanks, Jaans.

PS: I know there is an ERCF branch with StallGuard to provide an option to not need the toolhead filament sensor, but that doesn't suit me.

Ramalama2, 2023-05-03:
Hey, sorry for the Late reply.
- I wont make any changes  anymore, basically i dont make any Voron mods at all anymore xD
- The changes, ughhh that was so long ago, i dont remember even what i did, but actually not much. As far i remember i did initially this "Mod", because at the time, Eytecz didn't hat an option for the Hartk PCB and afterwards i remember that i modified everything a little bit, to make the mount Stiffer.
- But that changed, Eytecz has an Hart-PCB & Ercf + PCB Version now and i see no reasons to Stay on my Version actually.

Cheers :-)

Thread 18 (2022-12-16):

Chain_Anchor_2hole.stl can be replaced with stock 3 chain anchor?

Fett2, 2022-12-16:
Sorry to bring this up as an issue, but I wasn't sure where else to contact you. Can the stock chain anchor be used with the SB_LGXlitePCB? I have a 3 hole cable chain.

Loadmaster1, 2022-12-16:
The chains only need one of the screws at each end.  I used the most center one on my build.

JoaquinBerrios, 2022-12-31:
Yes, I'm using the stock three hole chain anchor, and it works fine.

Ramalama2, 2023-05-03:
Sorry for beeing Late, the Chainanchor is Original, so the default ones fits!

Closed 2023-05-03.

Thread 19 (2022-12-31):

SB_LGXlitePCB - Recommend cutting all pins flush on main hotend PCB to avoid shorts

JoaquinBerrios, 2022-12-31:
When using the mounting system from this repo on my main hotend PCB, the pins on the back of the board shorted against the metal housing of the motor. I was lucky that the PSU overcurrent protection tripped and nothing was damaged.

I would recommend noting on the instructions that it may be a good idea to trim all pins from the main hotend board flush (or at least the ones for the main plug near the motor housing) and that it may be a good idea to add some insulation between the PCB and the motor for additional safety. I just covered pins on the back of my board with a couple of layers of kapton tape after trimming the pins flush.

Ramalama2, 2023-05-03:
I did the same xD
And ill add that to the description, thanks!

Closed 2023-05-03.

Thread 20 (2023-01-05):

SB_LGXlitePCB - Cable Cover Test1 Doesn't Fit With Connector Plugs

D1rect10ns, 2023-01-05:
Feedback on the cable cover test1. It fits perfectly without the probe, FS, main 14-pin plug, or led plugs connected into the board, however with those connectors plugged in the cable cover won't close. It printed fine and doesn't seem too thin.

Thanks for the great projects Ramalama2! Lovin' your work!

Ramalama2, 2023-05-03:
Np, i know that the cover doesn't fit, just dunno if i should delete it or not, if ill delete it, then ill take away the opportunity to fix the Cover a little.
Dunno, but i definitively wont do a proper one, because it makes simply no sense for me.
One one hand im doing a whole new printer for myself, that will be not attractive to anyone, because it will be expensive as fuck.
On the other side i've realized that the LGX Lite isn't as nice/good as i hoped initially as i made this "Mod"...
I cant even say that ive made this mod, because its just a modification actually of Eytecz one...

Im anyway out of Voron Mods or Voron in general. As everyone already realized xD
But thanks for the Kudos :-)

Closed 2023-05-03.

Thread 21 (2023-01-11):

BedPan Wago mounts to small

BigDaddyV123, 2023-01-11:
I have wago 221 mounts I brought recently. Their widths 15.75mm wide. The bedpan's wago width is 12.6 mm. There appears to be enough space to fit 6 wider wago mounts

BigDaddyV123, 2023-01-11:
To update my issue. I come to find out that there are different kinds of two wire 221 mounts. There is 221-412, 221-612, 221-482, and 221-485. I think this design is for 221-412. It appears, for the orange two wire mounts (221-412, and 221-612) the difference is the max wire that can be used. 221-412 has a max wire size of 12, while the 221-612 has a max wire size of 10. This means that the 221-612 is larger than the 221-412, and thus will not fit in the BedPan. Can the BOM be updated to reflect the correct two wire 221 mount please.

Closed 2023-05-03.

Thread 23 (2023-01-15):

Bucket Sizes

D1rect10ns, 2023-01-15:
On my Voron 2.4 - 300, the measurement between my bed and chain is 74.13mm, so ideally a bucket size of 73.5 would work. Unfortunately the buckets in the STL folder don't go this small in size. Would it be possible to create some smaller sized buckets please?

D1rect10ns, 2023-01-18:
Closing this one out as I moved the whole bed forward to accommodate the purge bucket (not quite sure why I didn’t think of that!).

Closed 2023-01-18.

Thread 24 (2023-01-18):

Option_without_LGXlite-FanPCB - Works

kwojcik9, 2023-01-18:
This isn’t an issue, just wanted to say Option_without_LGXlite-FanPCB front cover works like a charm.  Thanks so much!

tagy, 2023-04-02:
I'm guessing you don't screw the PCB down with this version? As the holes will not line up? Is that right?

kwojcik9, 2023-04-02:
Hmm weird, I was able to screw down the PCB.  I know there are a few different versions.

Closed 2023-05-03.

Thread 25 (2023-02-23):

Define brush location

rmilyard, 2023-02-23:
I am looking at the Macro for Decontaminator Purge Bucket & Nozzle Scrubber.  I have my brush at rear (y) and center (x).  Not sure in marco how I change scrub location.

Ramalama2, 2023-05-03:
But its defined in his Macro, even with a picture.
[macro-purgebucket.cfg.zip](https://github.com/Ramalama2/Voron-2-Mods/files/11384452/macro-purgebucket.cfg.zip)

Thats my slightly modified macro for my 350.
But no one should use it as it is, you have to adjust the variables anyway, because everyones Y is different, even if the brush itself is perfectly centered.
Even while the Brush itself is perfectly centered, everyones center is different either, because of the endstop tolerances/endstop variations.

Cheers

Closed 2023-05-03.

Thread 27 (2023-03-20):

Upper Left and Upper Right belt clamps have cutouts in weird spots

TamaBaka, 2023-03-20:
This is kind of a nitpick more than anything since the belt is securely held either way.

Take the upper left belt clamp for instance.  Assuming that the small hole goes in the back, and the groove for the belt is at the bottom, there is a cutout on the left side.  I think this cutout should be on the right to give the belt space to drop in and route to the groove at the bottom.

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

TamaBaka, 2023-03-23:
An alternate way of looking at it is that it gives a space for the belt to loop back around.

Closed 2023-03-23.

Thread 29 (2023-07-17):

Mulit body front covers for multi color prints

chris155hp, 2023-07-17:
if you could make a multi body idler covers so that the logo can be printed a different color that would be amazing. Multi body has really become mainstream since the release of V0.2. The 0.2 skirts have mulit body in the Voron official git

scul86, 2023-07-19:
I did some work on the Henrikssn Cover to make them multibody and eliminate the pin holes.

Full disclosure, I have not printed these yet (up soon), but they match the other 'stock' covers in dimension and lack of pin holes.
[Henrikssn_Cover_multibody.zip](https://github.com/Ramalama2/Voron-2-Mods/files/12089850/Henrikssn_Cover_multibody.zip)

Closed 2023-08-18.

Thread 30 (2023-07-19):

Clarify number of Z-Belt-Clamps needed for the Front Idlers

scul86, 2023-07-19:
The filename of the `Front-Idlers_Z-Belt-Clamp-Upper-Left_x2` and `Front-Idlers_Z-Belt-Clamp-Upper-Right_x2` suggest that 2 of each should be printed, but then the instructions only seem to mention 2 of the modified clamps are required (1 each of left and right).

Ramalama2, 2023-07-21:
That depends on the version you're using, the normal version which i recommend, uses both 2x

The alternative ge5c Version, is different. But i thought i mentioned it somewhere. I think that's what you mean with the instructions.

scul86, 2023-07-22:
Yea, normal idlers, not the ge5c version.

By instructions, I meant the `Explosion_v2.pdf`.  That file specifies for each idler:
- 1x stock Voron lower clamp
- 1x top clip provided in this repository.

I would assume the "provided clip" to be 1x of the `Front-Idlers_Z-Belt-Clamp-Upper-[Left|Right]_x2.stl` depending on which side that idler is intended for.
I just don't see where the second clamp (specified in the filename w/ ***x2***) would go.

What makes sense in my mind for the full gantry would be:
- 4x stock Voron lower clamp
- 2x stock Voron upper clamp (for A/B motor mounts)
- 1x Front-Idlers_Z-Belt-Clamp-Upper-Left_x2.stl
- 1x Front-Idlers_Z-Belt-Clamp-Upper-Right_x2.stl

Is my above assumption wrong?  I am about to start my first v2.4 build, so I've not been able to try various combinations.

Ramalama2, 2023-07-23:
Aaah, yeah i was a bit stupid after 2 years xD

4x stock Voron lower clamp
2x stock Voron upper clamp (for A/B motor mounts)
1x Front-Idlers_Z-Belt-Clamp-Upper-Left.stl
1x Front-Idlers_Z-Belt-Clamp-Upper-Right.stl

Additionally:
2x Front-Idlers_Housing-Cover.stl
2x Front-Idlers_Housing_30mmScrew.stl
2x Front-Idlers_Inlet-5.15mm_default.stl
2x Beta_Cover_Round.stl (or round or henrikkson etc)
That is correct.

But i would exchange the normal versions there with the nipplefix variant (the reason is, the nipples on the normal version can brake easily). If they brake that's not a big deal either, but not beautiful xD
So:
2x Nipplefix-Front-Idlers_Housing_30mmScrew.stl
2x Nipplefix-Front-Idlers_Housing-Cover.stl

However you said:
"I just don't see where the second clamp (specified in the filename w/ x2) would go."
"Front-Idlers_Z-Belt-Clamp-Upper-Left_x2.stl"

Where do you see that filename? There is no filename with _x2 in the end...

scul86, 2023-07-23:
Huh, strange... Could have sworn they were in the filenames that I cloned from this repo.  Should have double checked the live repo first.

I'll have to double check tomorrow when I get home.

scul86, 2023-07-24:
yea, no idea where that `_x2` came from in my copies of the files.  I don't remember changing them, but must have.

Re-cloned the repo to a new location, and there were no `_x2` designations.

Closed 2023-07-24.

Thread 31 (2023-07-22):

Mandala Rose Works Bed Pan Smaller Distance

pjchaffin, 2023-07-22:
Is there any way to modify this design to suit distances from bed to chain all the way down to 72.5mm?

Closed 2023-07-22.

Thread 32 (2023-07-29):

Cura Slicer Profil

Martin11180, 2023-07-29:
Hello
Thanks for your Voron 2 mods
You can also make your Cura profile for ABS available via Github
It's hard to find on the web

greet
Martin

Ramalama2, 2023-08-02:
Hey Martin, im sorry, im not using any voron printer anymore, since the time i went the community.

I've switched to a Bambu x1c and this repository is more like an archive.
Didn't wanted to be an ass and delete it.

Sorry & Cheers

Closed 2023-08-18.

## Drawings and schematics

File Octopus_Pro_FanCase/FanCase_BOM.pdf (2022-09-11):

## 8x ST-FANSCREW

## FanCase_Top.stl

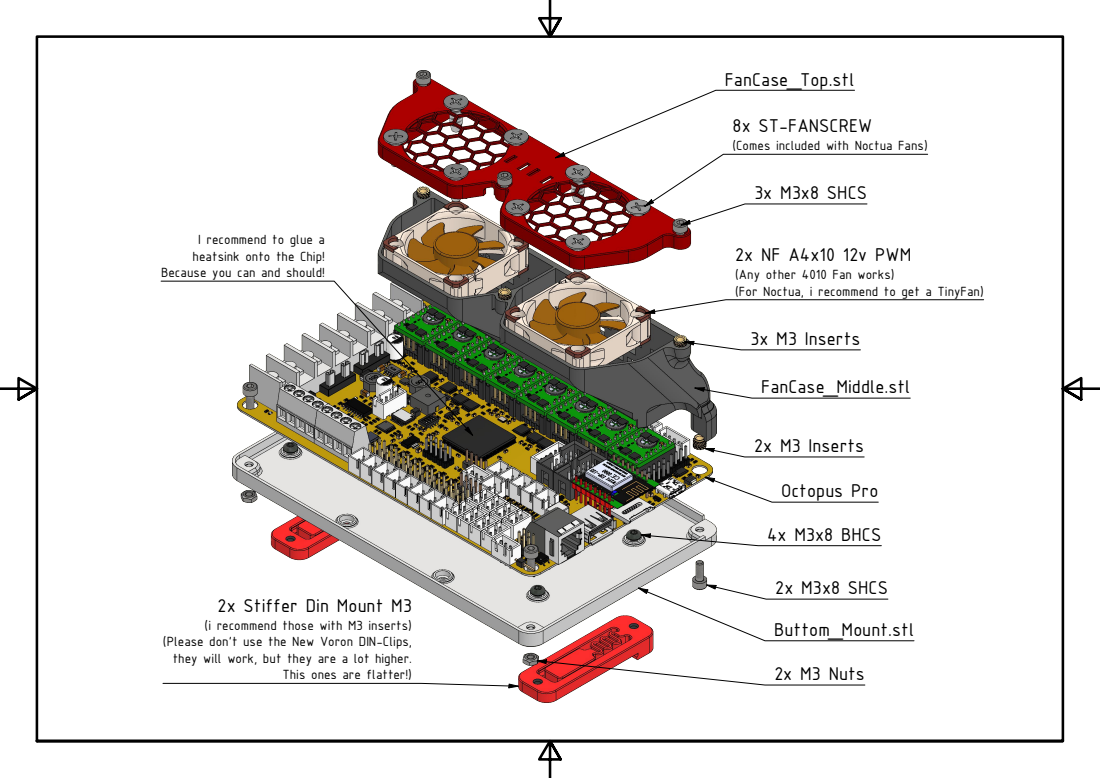
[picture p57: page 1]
3x M3x8 SHCS; 3x M3 Inserts; FanCase_Middle.stl; 2x M3 Inserts; Octopus Pro; 4x M3x8 BHCS; 2x M3x8 SHCS; 2x M3 Nuts; Buttom_Mount.stl

(Comes included with Noctua Fans)

I recommend to glue a
heatsink onto the Chip!
Because you can and should!

2x NF A4x10 12v PWM
(Any other 4010 Fan works)
(For Noctua, i recommend to get a TinyFan)

2x Stiffer Din Mount M3
(i recommend those with M3 inserts)

(Please don't use the New Voron DIN-Clips,
they will work, but they are a lot higher.

This ones are flatter!)

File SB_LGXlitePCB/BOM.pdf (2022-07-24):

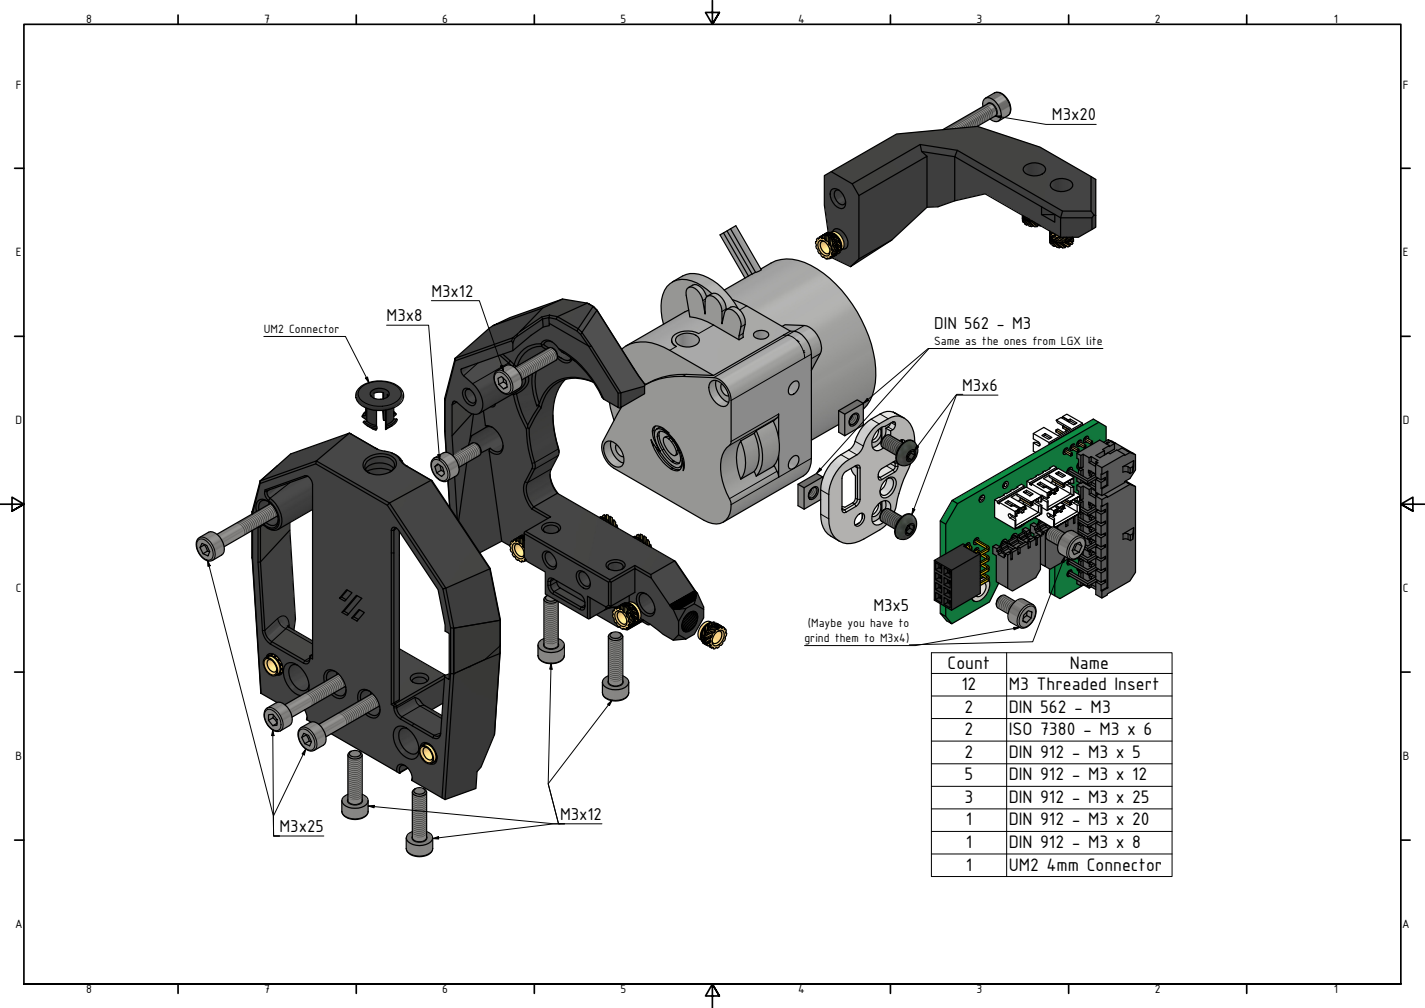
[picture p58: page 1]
UM2 Connector

DIN 562 - M3
Same as the ones from LGX lite

(Maybe you have to
grind them to M3x4)

Count | Name
12 | M3 Threaded Insert
2 | DIN 562 - M3
2 | ISO 7380 - M3 x 6
2 | DIN 912 - M3 x 5
5 | DIN 912 - M3 x 12
3 | DIN 912 - M3 x 25
1 | DIN 912 - M3 x 20
1 | DIN 912 - M3 x 8
1 | UM2 4mm Connector

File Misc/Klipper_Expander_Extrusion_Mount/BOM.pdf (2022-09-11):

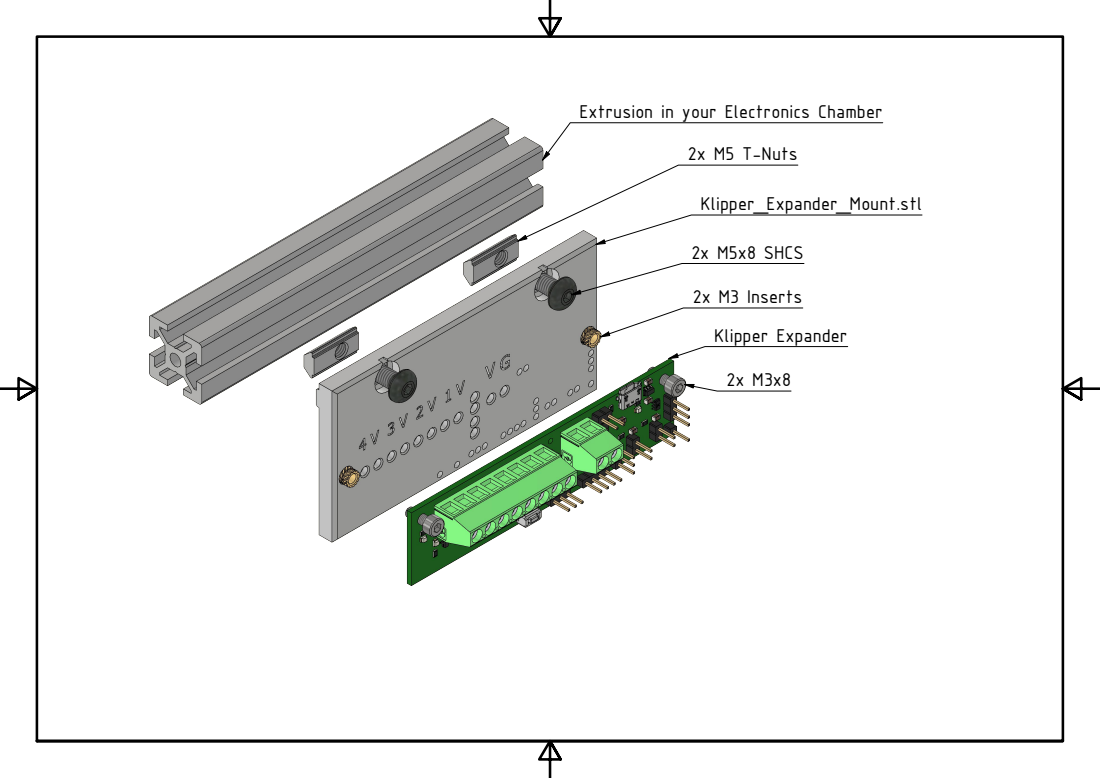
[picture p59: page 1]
2x M5x8 SHCS; 2x M5 T-Nuts; 2x M3 Inserts; Klipper Expander

Extrusion in your Electronics Chamber

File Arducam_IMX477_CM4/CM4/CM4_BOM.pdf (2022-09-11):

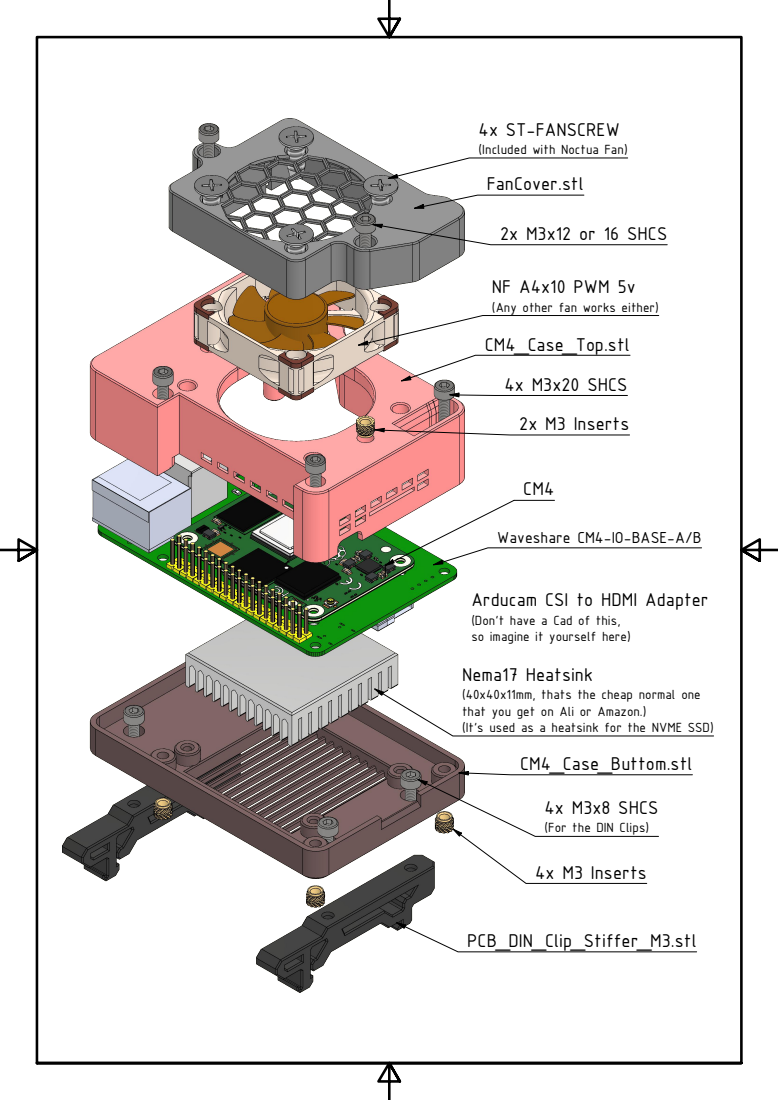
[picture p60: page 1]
2x M3x12 or 16 SHCS; 4x M3x20 SHCS; 2x M3 Inserts; 4x M3 Inserts

4x ST-FANSCREW
(Included with Noctua Fan)

NF A4x10 PWM 5v
(Any other fan works either)

Waveshare CM4-IO-BASE-A/B

Arducam CSI to HDMI Adapter
(Don't have a Cad of this,
so imagine it yourself here)

Nema17 Heatsink
(40x40x11mm, thats the cheap normal one
that you get on Ali or Amazon.)
(It's used as a heatsink for the NVME SSD)

4x M3x8 SHCS
(For the DIN Clips)

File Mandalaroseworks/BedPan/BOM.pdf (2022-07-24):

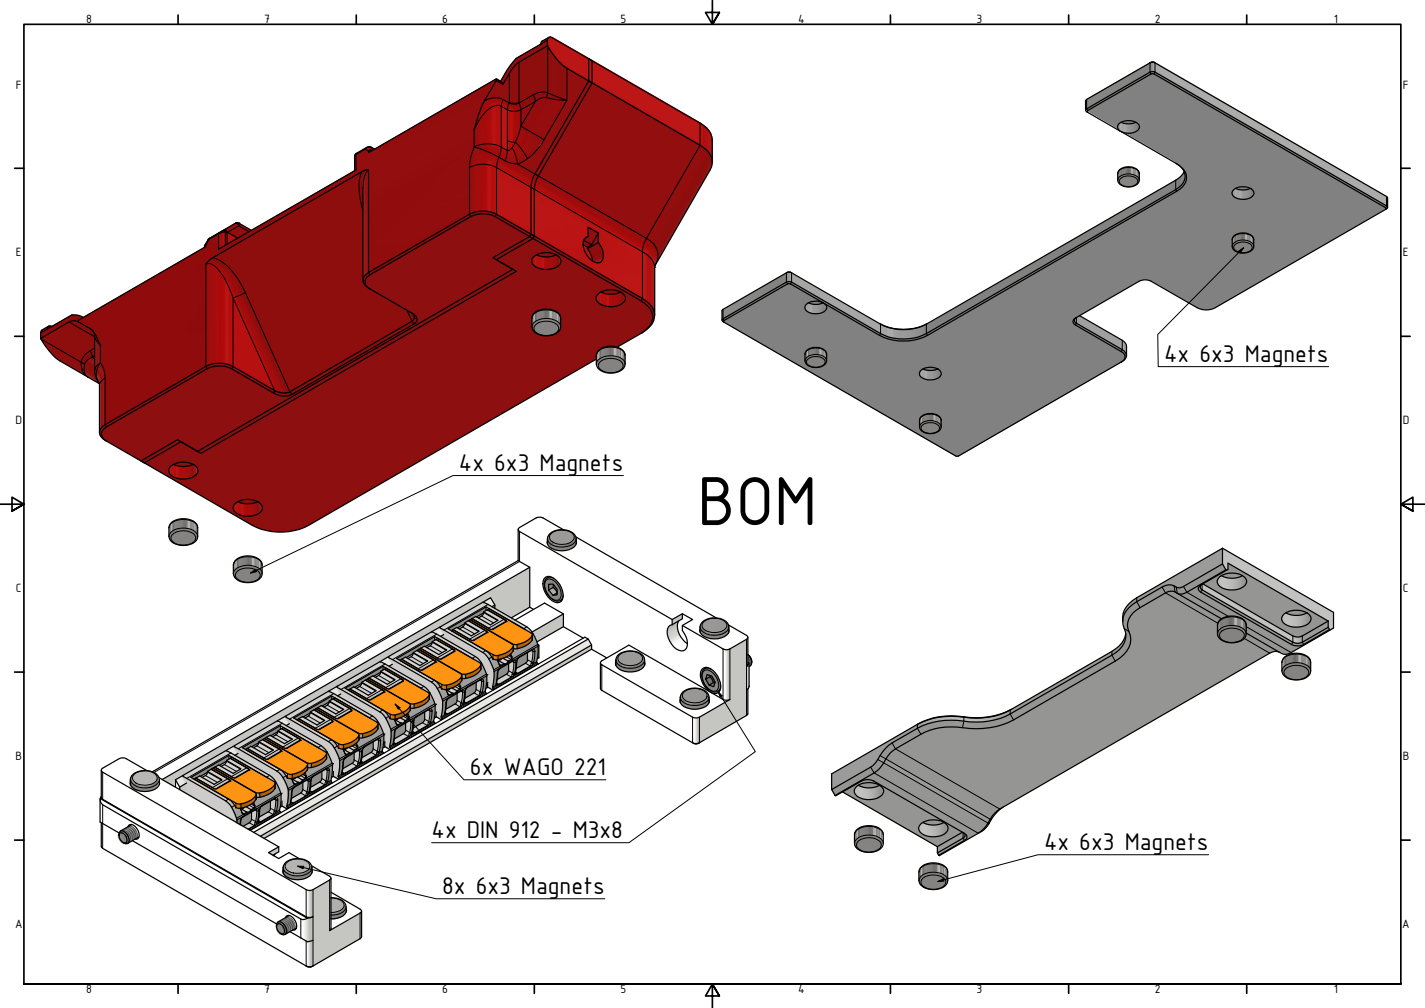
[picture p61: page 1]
4x DIN 912 - M3x8; 8x 6x3 Magnets; 4x 6x3 Magnets; 6x WAGO 221

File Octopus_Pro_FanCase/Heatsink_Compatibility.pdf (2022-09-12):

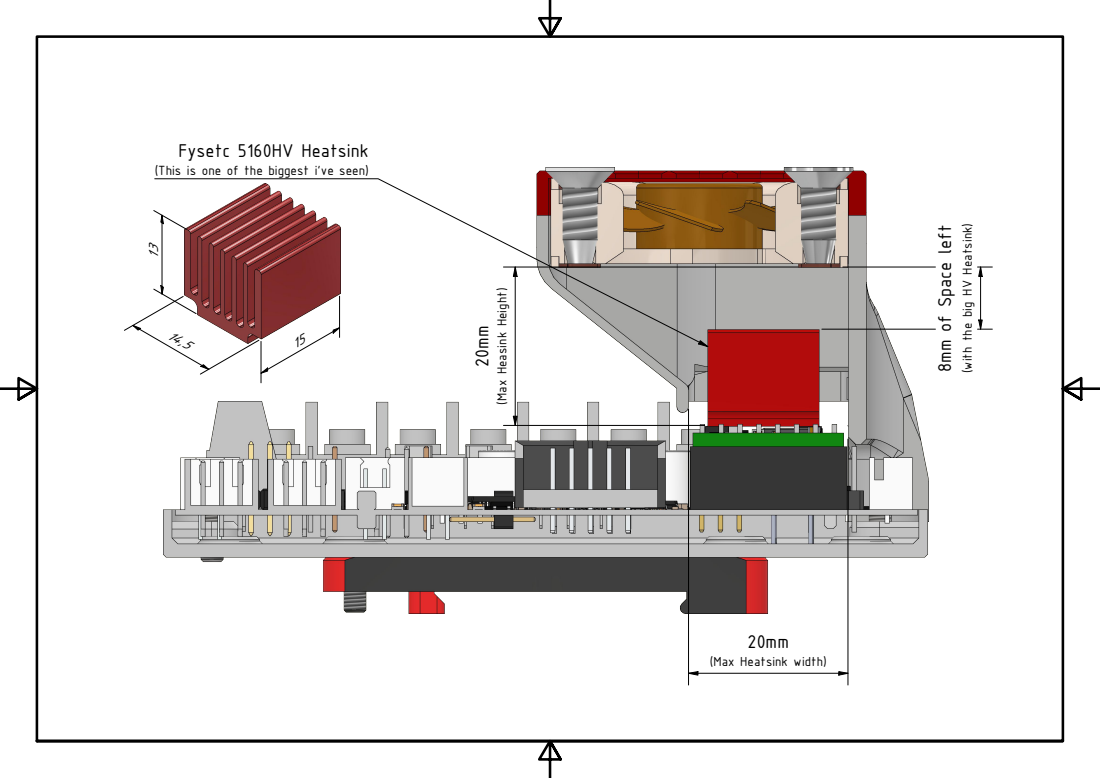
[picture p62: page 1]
ace left

Fysetc 5160HV Heatsink
(This is one of the biggest i've seen)

(with the big HV Heatsink)

(Max Heasink Height)

(Max Heatsink width)

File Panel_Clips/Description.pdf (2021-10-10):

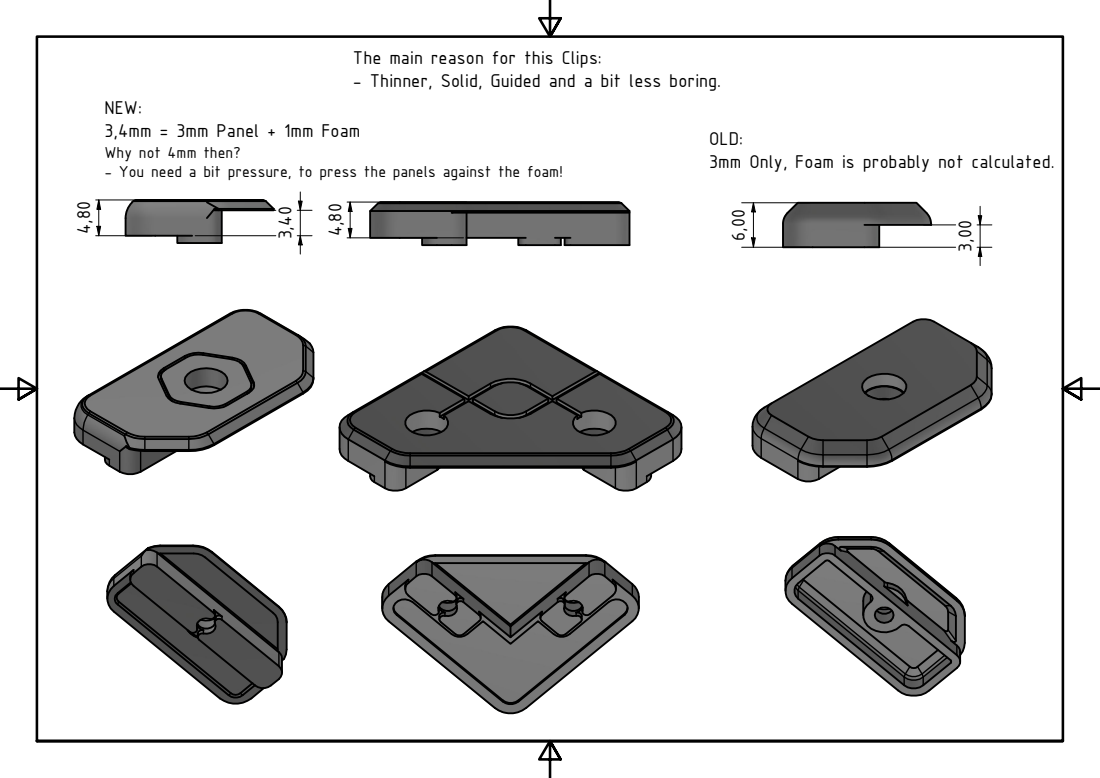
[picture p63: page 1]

The main reason for this Clips:
- Thinner, Solid, Guided and a bit less boring.

NEW:
3,4mm = 3mm Panel + 1mm Foam
Why not 4mm then?
- You need a bit pressure, to press the panels against the foam!

OLD:
3mm Only, Foam is probably not calculated.

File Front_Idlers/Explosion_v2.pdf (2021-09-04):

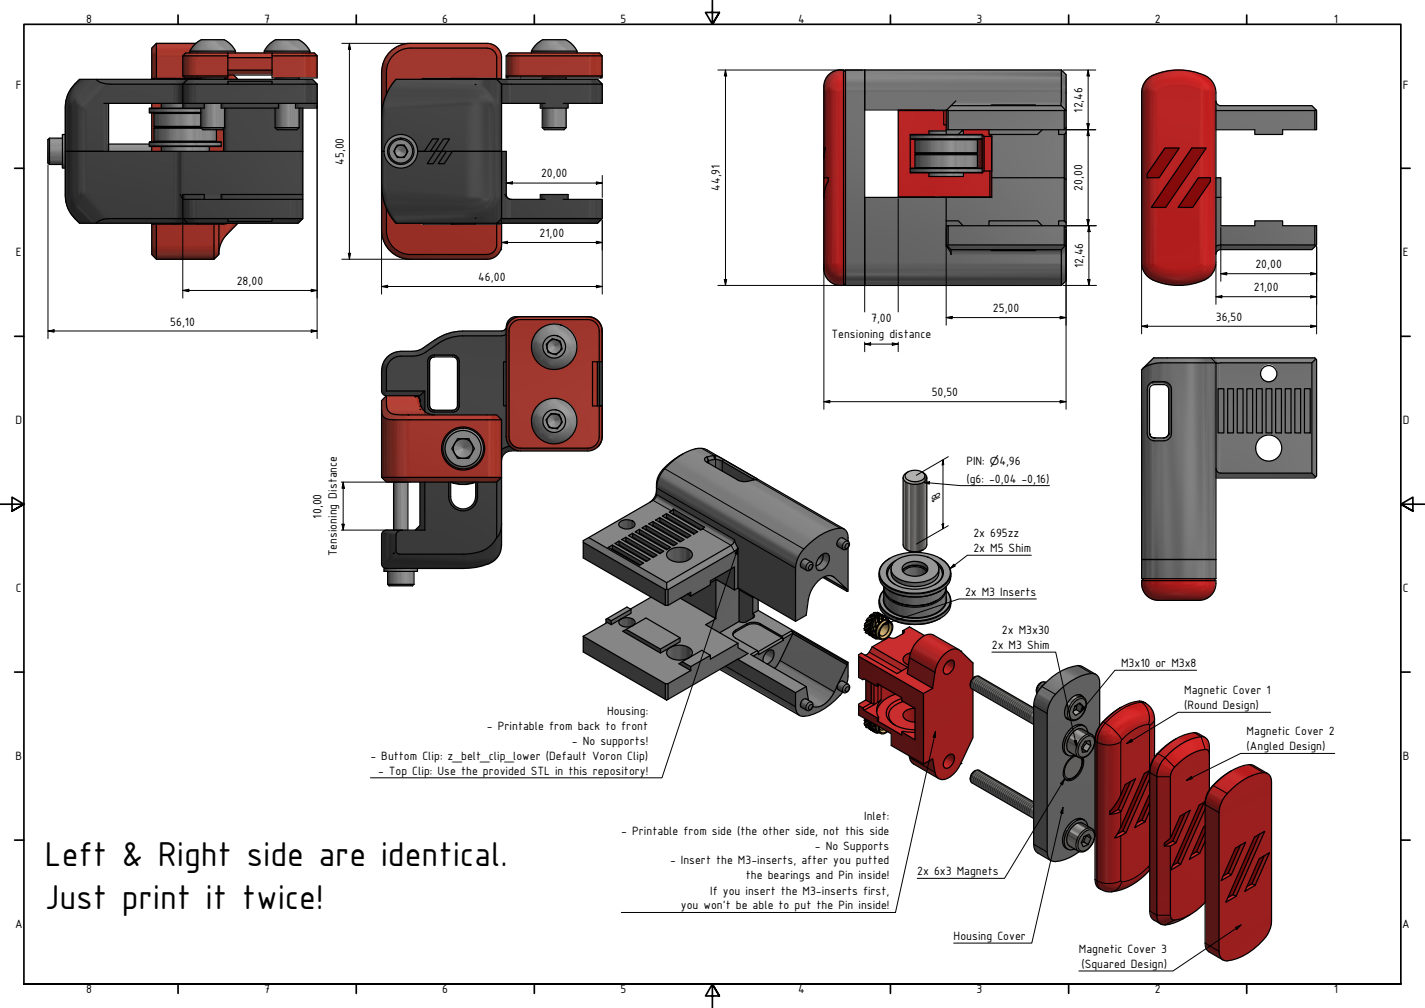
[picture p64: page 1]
- No supports!; 2x 695zz 2x M5 Shim; 2x M3 Inserts; - No Supports; 2x M3x30 2x M3 Shim; 2x 6x3 Magnets; Housing Cover; Magnetic Cover 1 (Round Design); Magnetic Cover 2 (Angled Design); Magnetic Cover 3 (Squared Design); Tensioning distance

- Printable from back to front

- Buttom Clip: z_belt_clip_lower (Default Voron Clip)
- Top Clip: Use the provided STL in this repository!

- Printable from side (the other side, not this side

Left & Right side are identical.
Just print it twice!

- Insert the M3-inserts, after you putted

the bearings and Pin inside!

If you insert the M3-inserts first,
you won't be able to put the Pin inside!

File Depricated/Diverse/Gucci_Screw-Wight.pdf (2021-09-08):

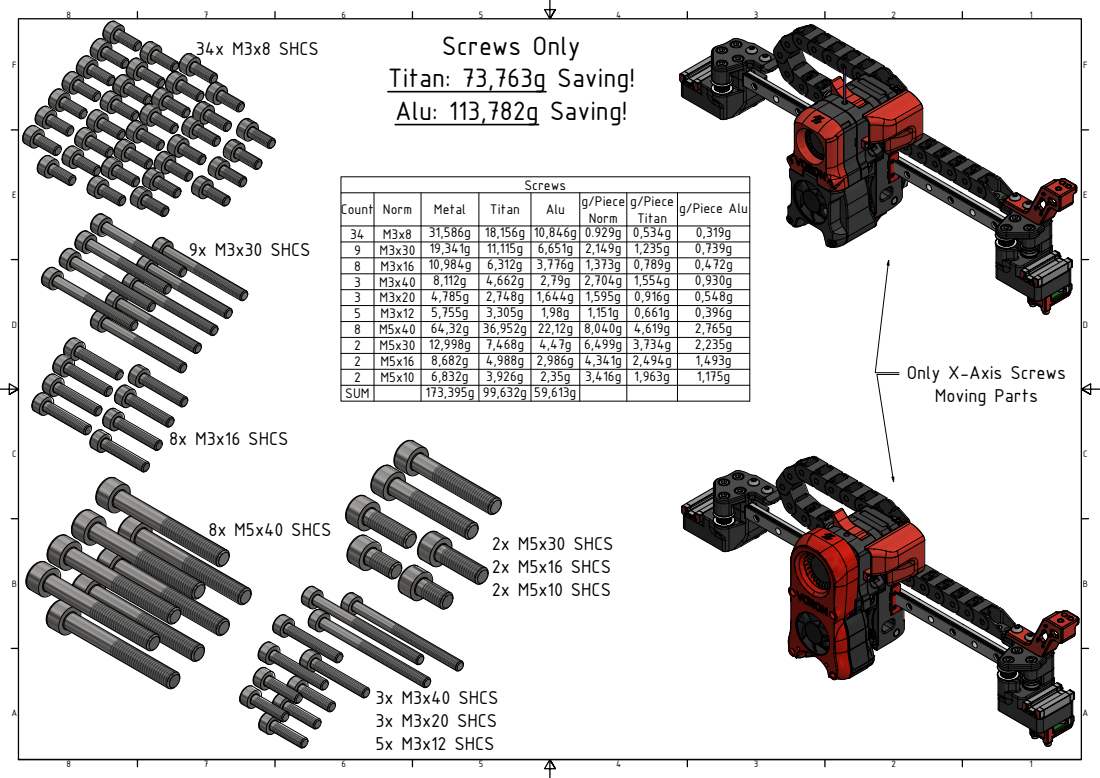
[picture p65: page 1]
34x M3x8 SHCS; 9x M3x30 SHCS; 8x M3x16 SHCS; 3x M3x40 SHCS 3x M3x20 SHCS 5x M3x12 SHCS; 8x M5x40 SHCS; 2x M5x30 SHCS 2x M5x16 SHCS 2x M5x10 SHCS; Count Norm; Metal; Titan; Alu; g/Piece Alu; SUM; Screws Only Titan: 73,763g Saving! Alu: 113,782g Saving!

Only X-Axis Screws
Moving Parts

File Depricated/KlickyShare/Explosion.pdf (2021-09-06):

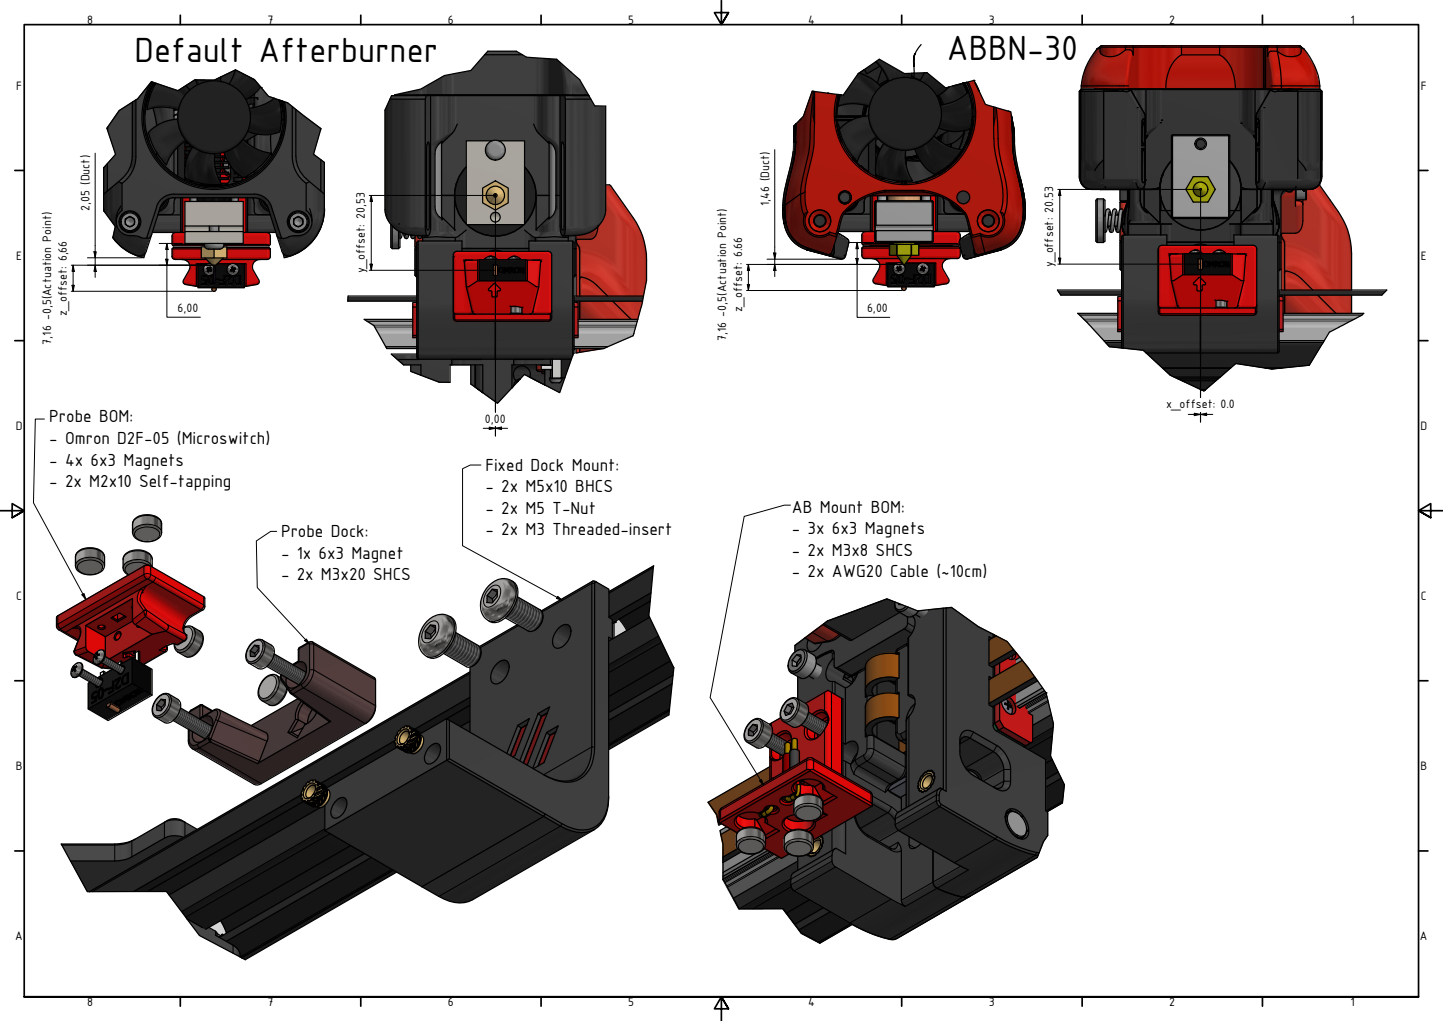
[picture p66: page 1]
Probe BOM: - Omron D2F-05 (Microswitch) - 4x 6x3 Magnets - 2x M2x10 Self-tapping; Probe Dock: - 1x 6x3 Magnet - 2x M3x20 SHCS; x_offset: 0.0; Default Afterburner; ABBN-30

Fixed Dock Mount:
- 2x M5x10 BHCS
- 2x M5 T-Nut
- 2x M3 Threaded-insert

AB Mount BOM:
- 3x 6x3 Magnets
- 2x M3x8 SHCS
- 2x AWG20 Cable (~10cm)

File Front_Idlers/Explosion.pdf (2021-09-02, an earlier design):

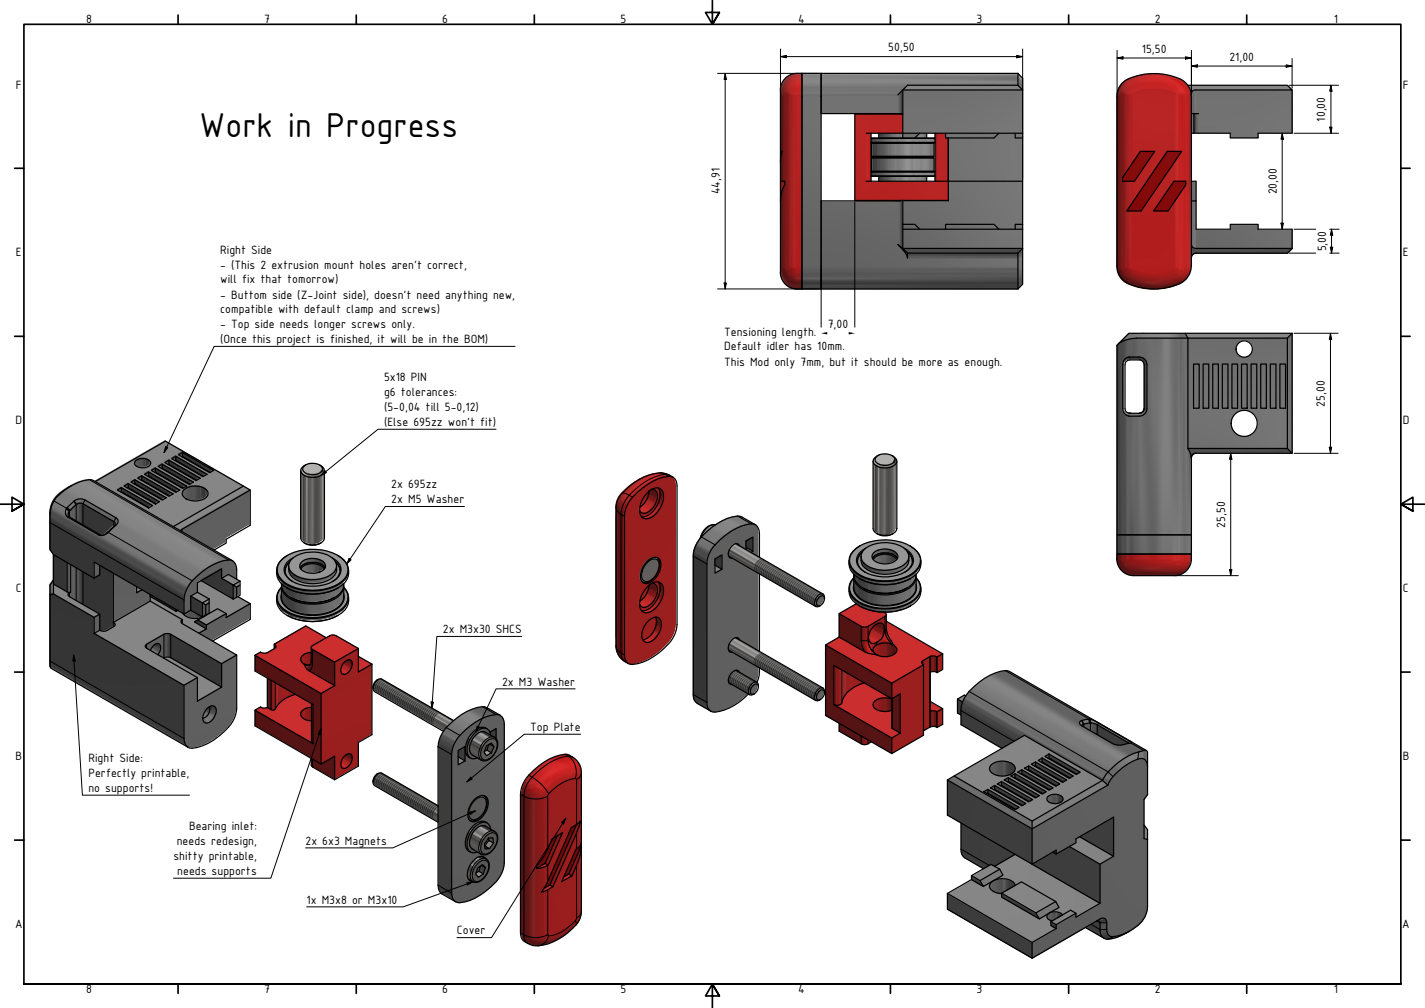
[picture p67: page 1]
2x 695zz 2x M5 Washer; Right Side: Perfectly printable, no supports!; Bearing inlet: needs redesign, shitty printable, needs supports; 2x M3x30 SHCS; 2x M3 Washer; 2x 6x3 Magnets; Top Plate

Work in Progress

Right Side
- (This 2 extrusion mount holes aren't correct,
will fix that tomorrow)
- Buttom side (Z-Joint side), doesn't need anything new,
compatible with default clamp and screws)
- Top side needs longer screws only.
(Once this project is finished, it will be in the BOM)

Tensioning length.
Default idler has 10mm.
This Mod only 7mm, but it should be more as enough.

5x18 PIN
g6 tolerances:
(5-0,04 till 5-0,12)
(Else 695zz won't fit)

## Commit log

2021-08-31 Initial Upload
    [AB_Connector_Plug_V2.1_JstXH.ipt, AB_Connector_Plug_V2.1_JstXH.stl, AB_Connector_Plug_V2.1_JstXH.stp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]
2021-08-31 Cable Clip
    [Misumi_Cable_Clip.ipt, Misumi_Cable_Clip.stl, Misumi_Cable_Clip.stp]
2021-09-01 RBPB5 Cad Files
    [6x3 Magnet.ipt, ANSI B18.3.4M - M5 x 0.8 x 22.ipt, Assembly-Explosion.stp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]
2021-09-02 Front Idlers
    [Assembly_Front-Idler-Right.stp, Cover_Magnetic_Hall.ipt]
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2021-09-03 Alpha Release!
    [Alpha_Cover_Angled.stl, Alpha_Cover_Round.stl, Alpha_Cover_Squared.stl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]
2021-09-03 Z-Belt_Clamp_Upper Added (Slightly modified Lower version)
    [Alpha_Z-Belt-Clamp-Upper.stl, Front-Idlers_Z-Belt-Clamp-Upper.ipt]
2021-09-04 Alternative (Printability test)
    [Alpha_Housing_2.stl, Alpha_Inlet_2.stl]
2021-09-04 Small Fix
    [Alpha_Inlet_2.stl]
2021-09-04 Ups, uploaded the wrong clip previously. This is the right one!
    [Alpha_Z-Belt-Clamp-Upper.stl, Assembly_Front-Idler-Right.stp, Front-Idlers_Z-Belt-Clamp-Upper.ipt]
2021-09-04 Old Cad File, just if someone is interrested
    [Assembly_Front-Idler-Right.stp]
2021-09-04 Release :-)
    [Alpha_Cover_Angled.stl, Alpha_Cover_Round.stl, Alpha_Cover_Squared.stl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]
2021-09-05 Final Release of Front-Idlers!
    [Front-Idlers_Housing.ipt, Front-Idlers_Housing.stl]
2021-09-06 Mounting Fix, Belt alignment
    [Front-Idlers_Housing.ipt, Front-Idlers_Housing.stl, Front-Idlers_Housing.stp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]
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2021-09-13 Small Crap
    [eSun_Holder.ipt, eSun_Holder.stl]
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2021-09-14 Nevermore RLF-35
    [Nevermore_RLF35-v2.stp]
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2021-09-27 RBPB5 Final Mod!
    Final Release!
    [Assembly-Explosion.stp, Cover_Magnetic_Hall.ipt, Cover_Magnetic_Hall.stp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]
2021-09-27 Added Cover + 40mm Housing: RELEASE!
    [Alpha_Cover_Angled.stl, Alpha_Cover_Round.stl, Alpha_Cover_Squared.stl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]
2021-09-27 Nevermore, second try
    [Nevermore_RLF35-v2.stp]
2021-09-28 Move Assembly to old, to avoid confusion
    [Assembly_Front-Idlers_v2.stp]
2021-09-29 Test 4
    [Nevermore_RLF35-v4.step]
2021-10-02 Nevermore Test 1 - LID
    [Nevermore_RLF35-v4.step, Release_Nevermore-RLF35_Base.stp, Testing_Nevermore-RLF35_LID.stp]
2021-10-02 Nevermore Printing Fix
    [Testing_Nevermore-RLF35_LID.stp]
2021-10-02 Fixed the LID
    [Release_Nevermore-RLF35_LID.stp, Testing_Nevermore-RLF35_LID.stp]
2021-10-10 Panel Clips Release
    [Clip_Corner.ipt, Clip_Corner.stp, Clip_Corner_4mm.stl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]
2021-10-10 Small Improvement
    [Clip_Corner.ipt, Clip_Corner_4mm.stl, Clip_Normal.ipt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]
2021-10-10 Doors Part 1
    [Door_Handle.ipt, Door_L_4mm.stl, Door_Latch.ipt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]
2021-10-11 Door Hinges 4mm
    [Assembly_Doorhinge.iam, Clip_Corner.ipt, Clip_Normal.ipt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]
2021-10-12 Forgot the other side (Doorhinge)
    [Doorhinge_Outlet_L.stl, Doorhinge_Outlet_R.stl]
2021-10-12 Doorhinge_Inlet (small printability update)
    [Doorhinge_Inlet.0003.ipt, Doorhinge_Inlet.ipt, Doorhinge_Inlet.stl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]
2021-10-12 Final Version of Door Hinges!
    [Doorhinge_Inlet.ipt, Doorhinge_Inlet.stl, Doorhinge_Inlet.stp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]
2021-10-12 ups, forgot sth, this is the final of the inlet xD
    [Doorhinge_Inlet.ipt, Doorhinge_Inlet.stl, Doorhinge_Inlet.stp]
2021-10-13 Offcentered Version (Use it after installation, not directly)
    [Door_Latch-Offcentered.ipt, Door_Latch-Offcentered.stl, Door_Latch-Offcentered.stp]
2021-10-15 Front Idler Cover Update
    [Alpha_Cover_Angled.stl, Alpha_Cover_Round.stl, Alpha_Cover_Squared.stl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]
2021-10-17 DeeperKlicky Bucket
    [Bucket_350_Klicky_Deeper.stp, Bucket_350_Klicky_Deeper2.stp]
2021-10-17 Deeper Bucket
    [Bucket_350_Klicky_Deeper.stl, Bucket_350_Klicky_Deeper2.stl]
2021-10-17 Screwed Handle
    [Randell-Door_Handle.ipt]
2021-10-17 Randell Version Handle (Screwed)
    [Randell-Door_Handle.stp]
2021-10-19 Stiffer Klicky for Testings
    [Stiffy-Klicky.ipt, Stiffy-Klicky.stl, Stiffy-Klicky.stp]
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2021-10-19 Ge5c Special
    [BETA_Front-Idlers_Inlet_2mmShorter.stl]
2021-11-04 Front Idlers small update
    [Front-Idlers_Inlet-5.0mm_pin_hole.stl, Front-Idlers_Inlet-5.1mm_pin_hole.3mf, Front-Idlers_Inlet-5.2mm_pin_hole.3mf]
2021-11-10 GE5C Version
    GE5C Version
    [BETA_Front-Idlers_Inlet_2mmShorter.stl, Front-Idlers_Housing_L.ipt, Front-Idlers_Housing_R.ipt]
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2021-11-17 Nevermore System
    [RLF35_Bottom.stl]
2022-03-22 Updates & Cleanups
    NEW: Voron Trident Front Idlers by TadasMit
    [AB_Connector_Plug_V2.1_JstXH.ipt, AB_Connector_Plug_V2.1_JstXH.stl, AB_Connector_Plug_V2.1_JstXH.stp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]
2022-03-22 Small Fixes
    [Adxl_Mount.0013.ipt, Extrusion_Inside.0001.ipt]
2022-03-23 Adding slowly sources
    [Front-Idlers_Inlet.ipt, Front-Idlers_Inlet.stp]
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2022-05-14 Fix "Deprecated" folder name
    [AdxlMount_v1.stl, Adxl_Mount.ipt, Adxl_Mount.stp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]
2022-07-24 MRW BadPan and Endstop!
    - New Z-Endstop
    - New Purgebucket/BedPan
    [Brush_Holder.ipt, Bucket+Magnets.iam, Bucket.stp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]
2022-07-24 SB LGX lite 2-Part PCB
    Release
    [Chain_Anchor_2hole.ipt, Chain_Anchor_2hole.stl, Chain_Anchor_2hole.stp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]
2022-07-25 Nipplefix (Front-Idlers)
    [Assembly.iam, Front-Idlers_Housing-Cover.ipt, Front-Idlers_Housing.0018.ipt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]
2022-07-25 Cable Cover Test1
    [Cable_Cover_Test1.ipt, Cable_Cover_Test1.stl, Cable_Cover_Test1.stp]
2022-08-11 Create Henrikssn_Cover-Nipplefix.stl
    Put the Nipplefix receptacles on the back of the Henrikssn cover.
    [Henrikssn_Cover-Nipplefix.stl]
2022-09-11 Update Part 1
    [CM4_BOM.dwg, CM4_Case_Buttom.ipt, CM4_Case_Buttom.stl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]
2022-09-11 KEEM Release
    [Assembly.dwg, Assembly.iam, Klipper_Expander_Mount.ipt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]
2022-09-11 Update Part 2
    [Buttom_Mount.ipt, Buttom_Mount.stl, Buttom_Mount.stp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]
2022-09-12 Heatsink Compatibility
    [Heatsink5160Pro.ipt]
2022-09-12 ISDT c4 Charger
    [FanCover.ipt, Feets.ipt, Housing.iam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]
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2022-10-21 Added a blank variant of the BedPan cable holder for people with different wago wiring
    [Cableholder-blank.stl]
2023-01-13 Modified Bedpan to suit Non-MRW Beds.
    I modified the bedpan to suit not MRW Beds as the stock one didn't fit (too long) and was too high which clashed with Sexbolt. Loss of 11.5mm in Bucket height but still the largest bucket I could find,.
    [Bucket_Non_MRW.step, Bucket_Non_MRW.stl]
2023-05-03 Update README.md
    User request to fix the wago name in the Bom
